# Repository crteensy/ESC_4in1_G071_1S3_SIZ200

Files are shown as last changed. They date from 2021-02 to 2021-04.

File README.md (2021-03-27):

# ESC_4in1_G071_1S3_SIZ200

## UNTESTED
The G071+NCP81161 combo was successfully tested (with PSMN1R8-30MLHX though).

## Important: mounting
The PCB is quite crowded around the mounting holes:
- Do not use M3 metal hardware.
- You can use M3 plastic with slim (5mm outer diameter) standoffs
- You can also use M2 with rubber grommets

## Description
KiCad project for a 20mm 4in1 ESC
- 4 layers for prototyping
- no part smaller than 0402
- 1-3 S
- should be abe to handle 15 A continuous
- STM32G071
- NCP81161 gate drivers
- SIZ200
- 0m5 current sense shunt with INA186A2
- 5V reg: TPS630701; max 2A (VBat = 5 V)

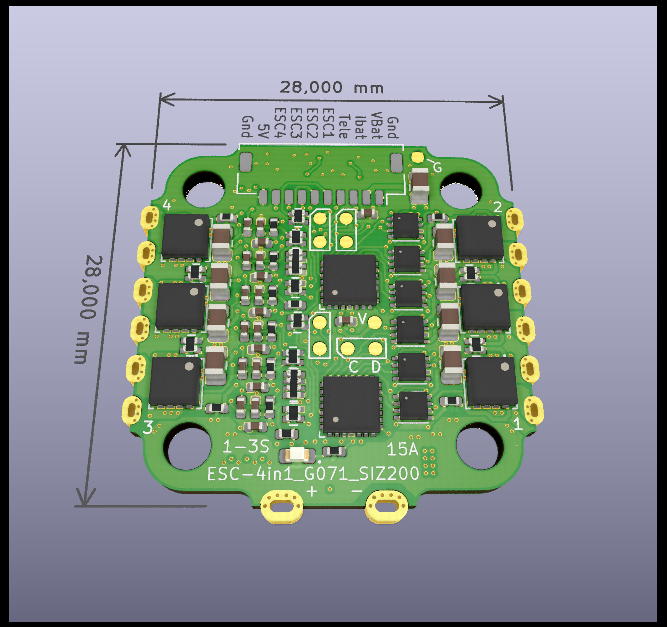
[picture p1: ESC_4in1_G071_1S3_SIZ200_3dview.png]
3D view top


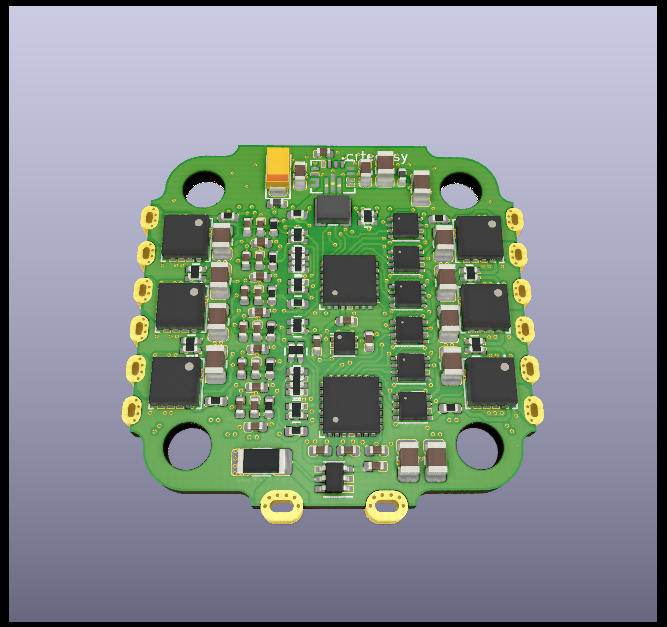
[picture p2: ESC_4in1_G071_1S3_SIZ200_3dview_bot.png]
3D view bottom


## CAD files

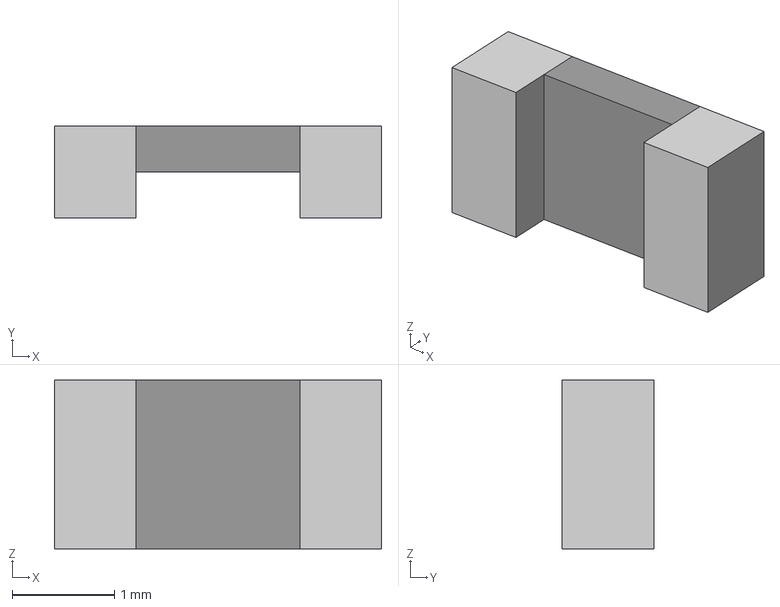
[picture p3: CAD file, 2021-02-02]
backup_20210413_badVias/mod/HCS1206_L500_stp.stp
3.20 x 0.9 x 1.65 mm

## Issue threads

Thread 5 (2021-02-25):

add silk screen for SWD pads

crteensy, 2021-02-25:
clock, data, and ESC# identification are missing for swd pads

Closed 2021-02-27.

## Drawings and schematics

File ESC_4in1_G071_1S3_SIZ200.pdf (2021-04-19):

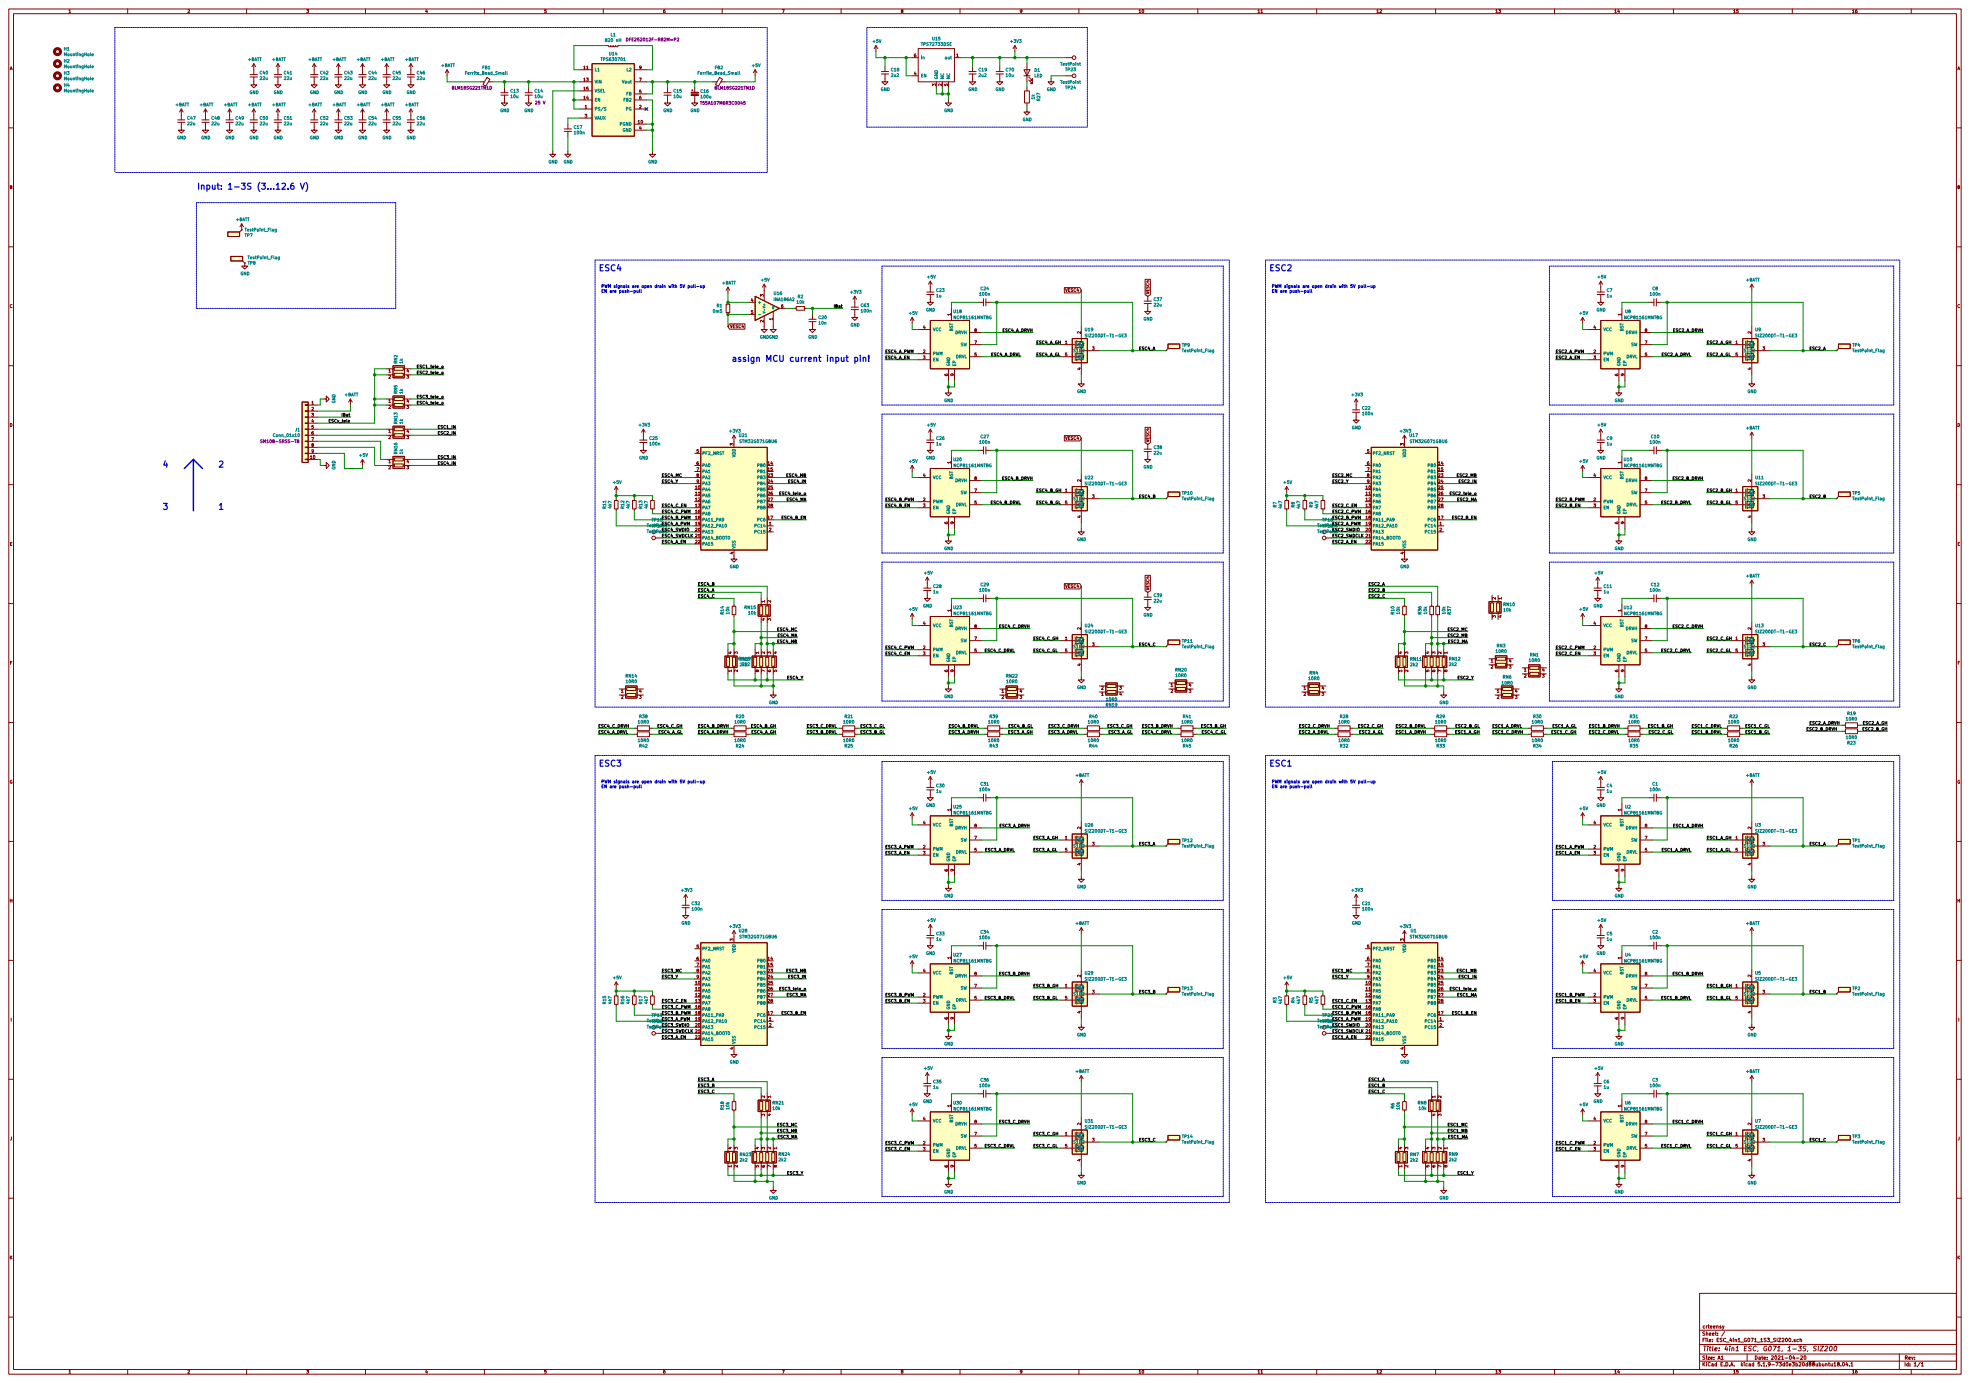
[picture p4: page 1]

PWM signals are open drain with 5V pull-up
EN are push-pull

assign MCU current input pin!

File: ESC_4in1_G071_1S3_SIZ200.sch Sheet: / crteensy

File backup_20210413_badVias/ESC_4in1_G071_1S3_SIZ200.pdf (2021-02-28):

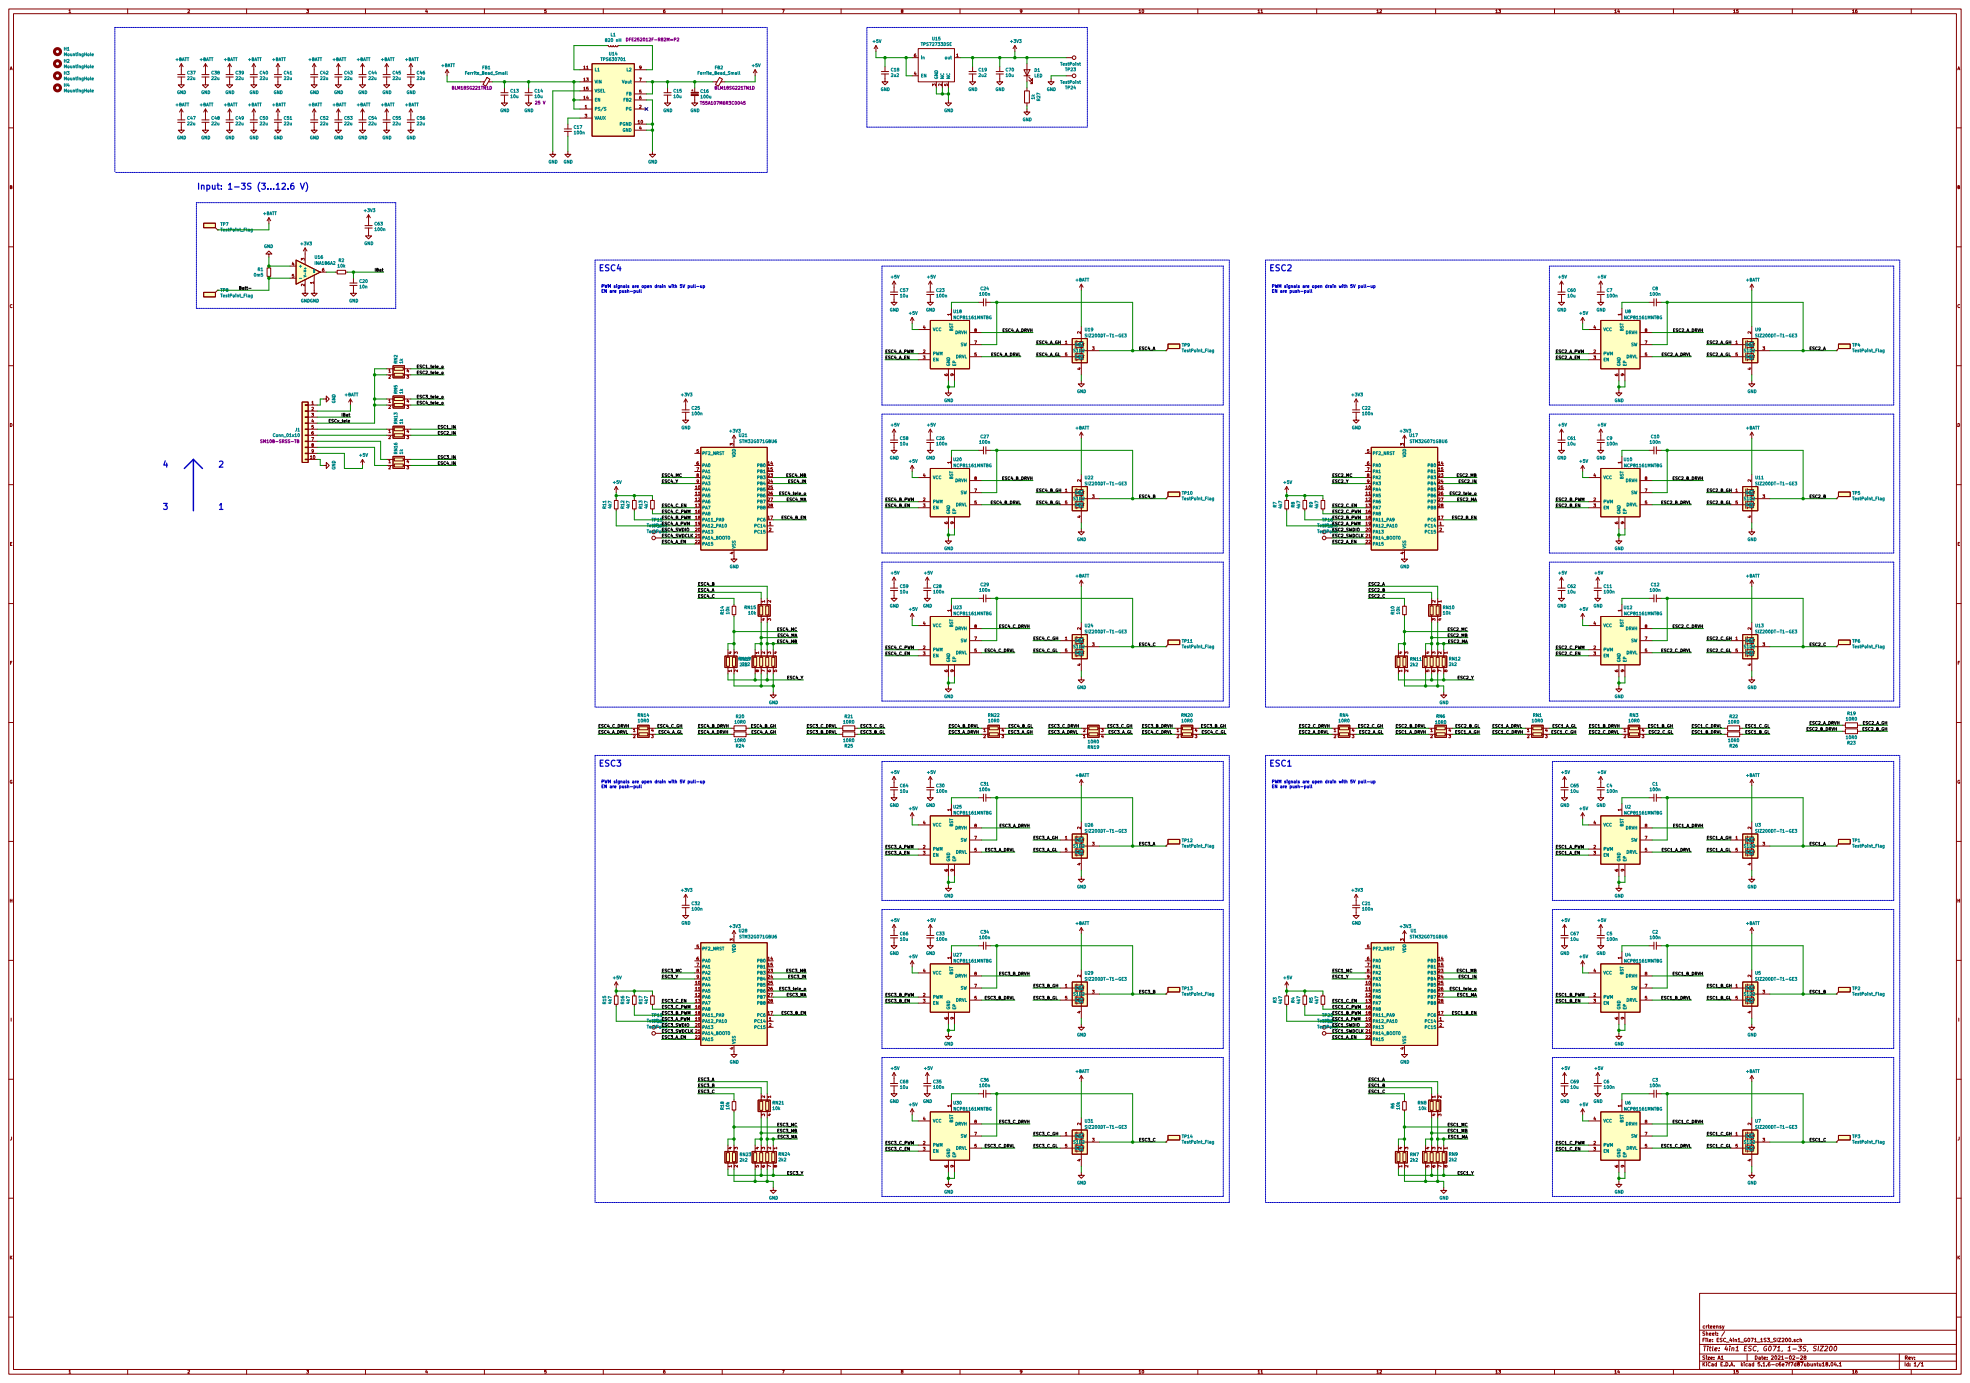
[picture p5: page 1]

PWM signals are open drain with 5V pull-up
EN are push-pull

ESC2_A_GL PWM signals are open drain with 5V pull-up

File: ESC_4in1_G071_1S3_SIZ200.sch Sheet: / crteensy

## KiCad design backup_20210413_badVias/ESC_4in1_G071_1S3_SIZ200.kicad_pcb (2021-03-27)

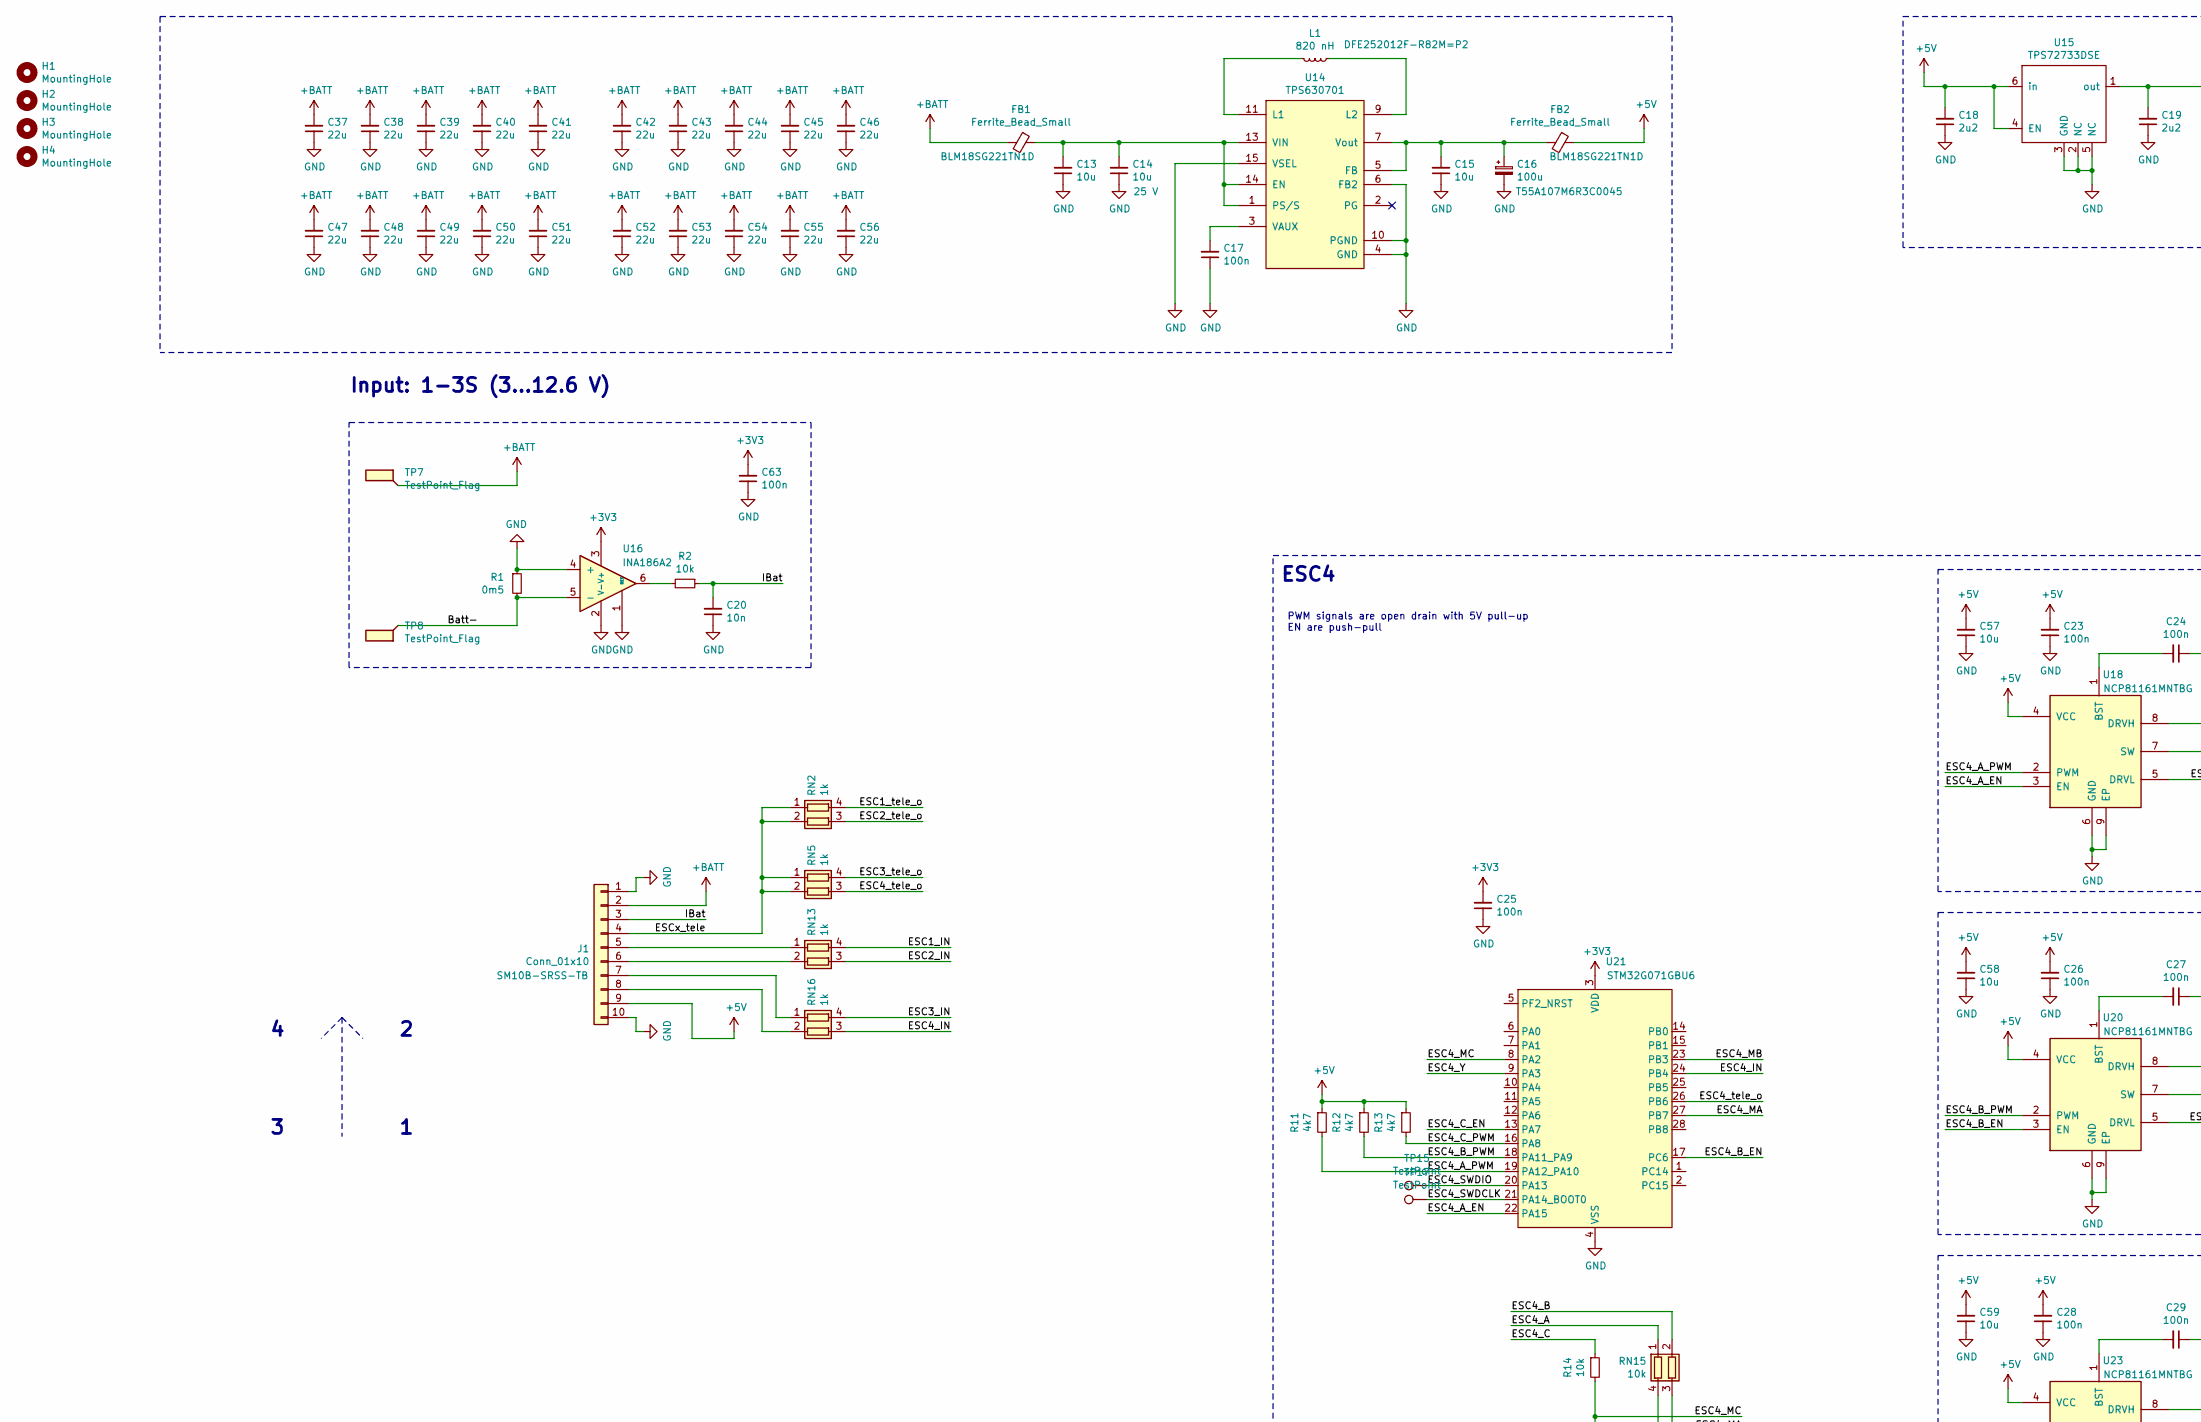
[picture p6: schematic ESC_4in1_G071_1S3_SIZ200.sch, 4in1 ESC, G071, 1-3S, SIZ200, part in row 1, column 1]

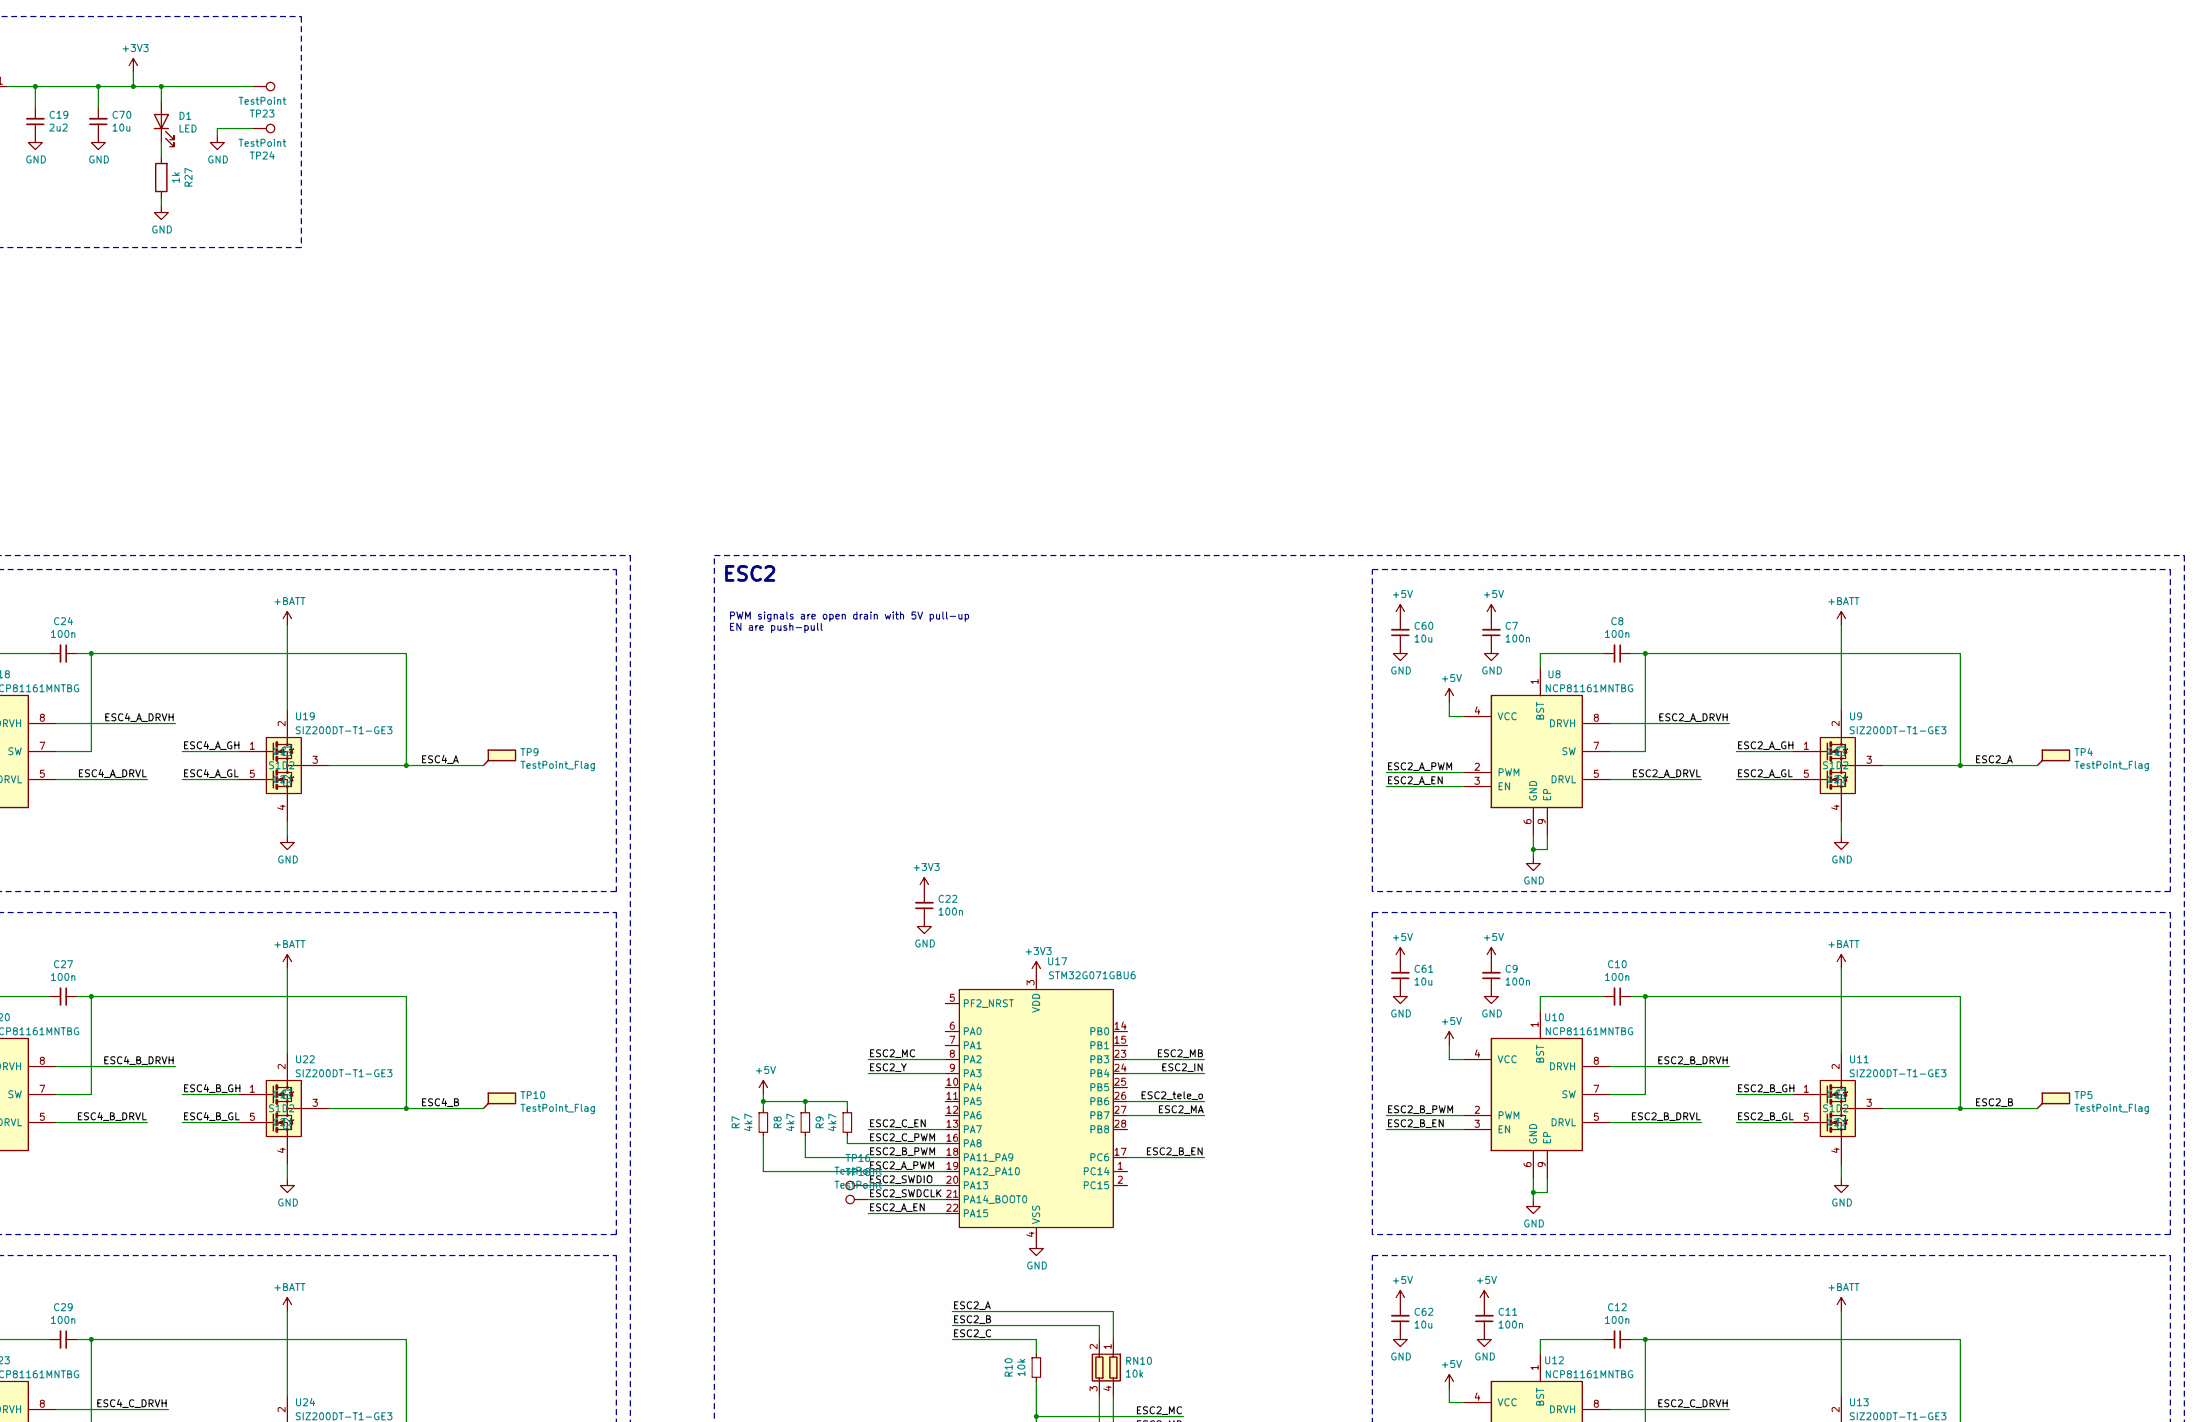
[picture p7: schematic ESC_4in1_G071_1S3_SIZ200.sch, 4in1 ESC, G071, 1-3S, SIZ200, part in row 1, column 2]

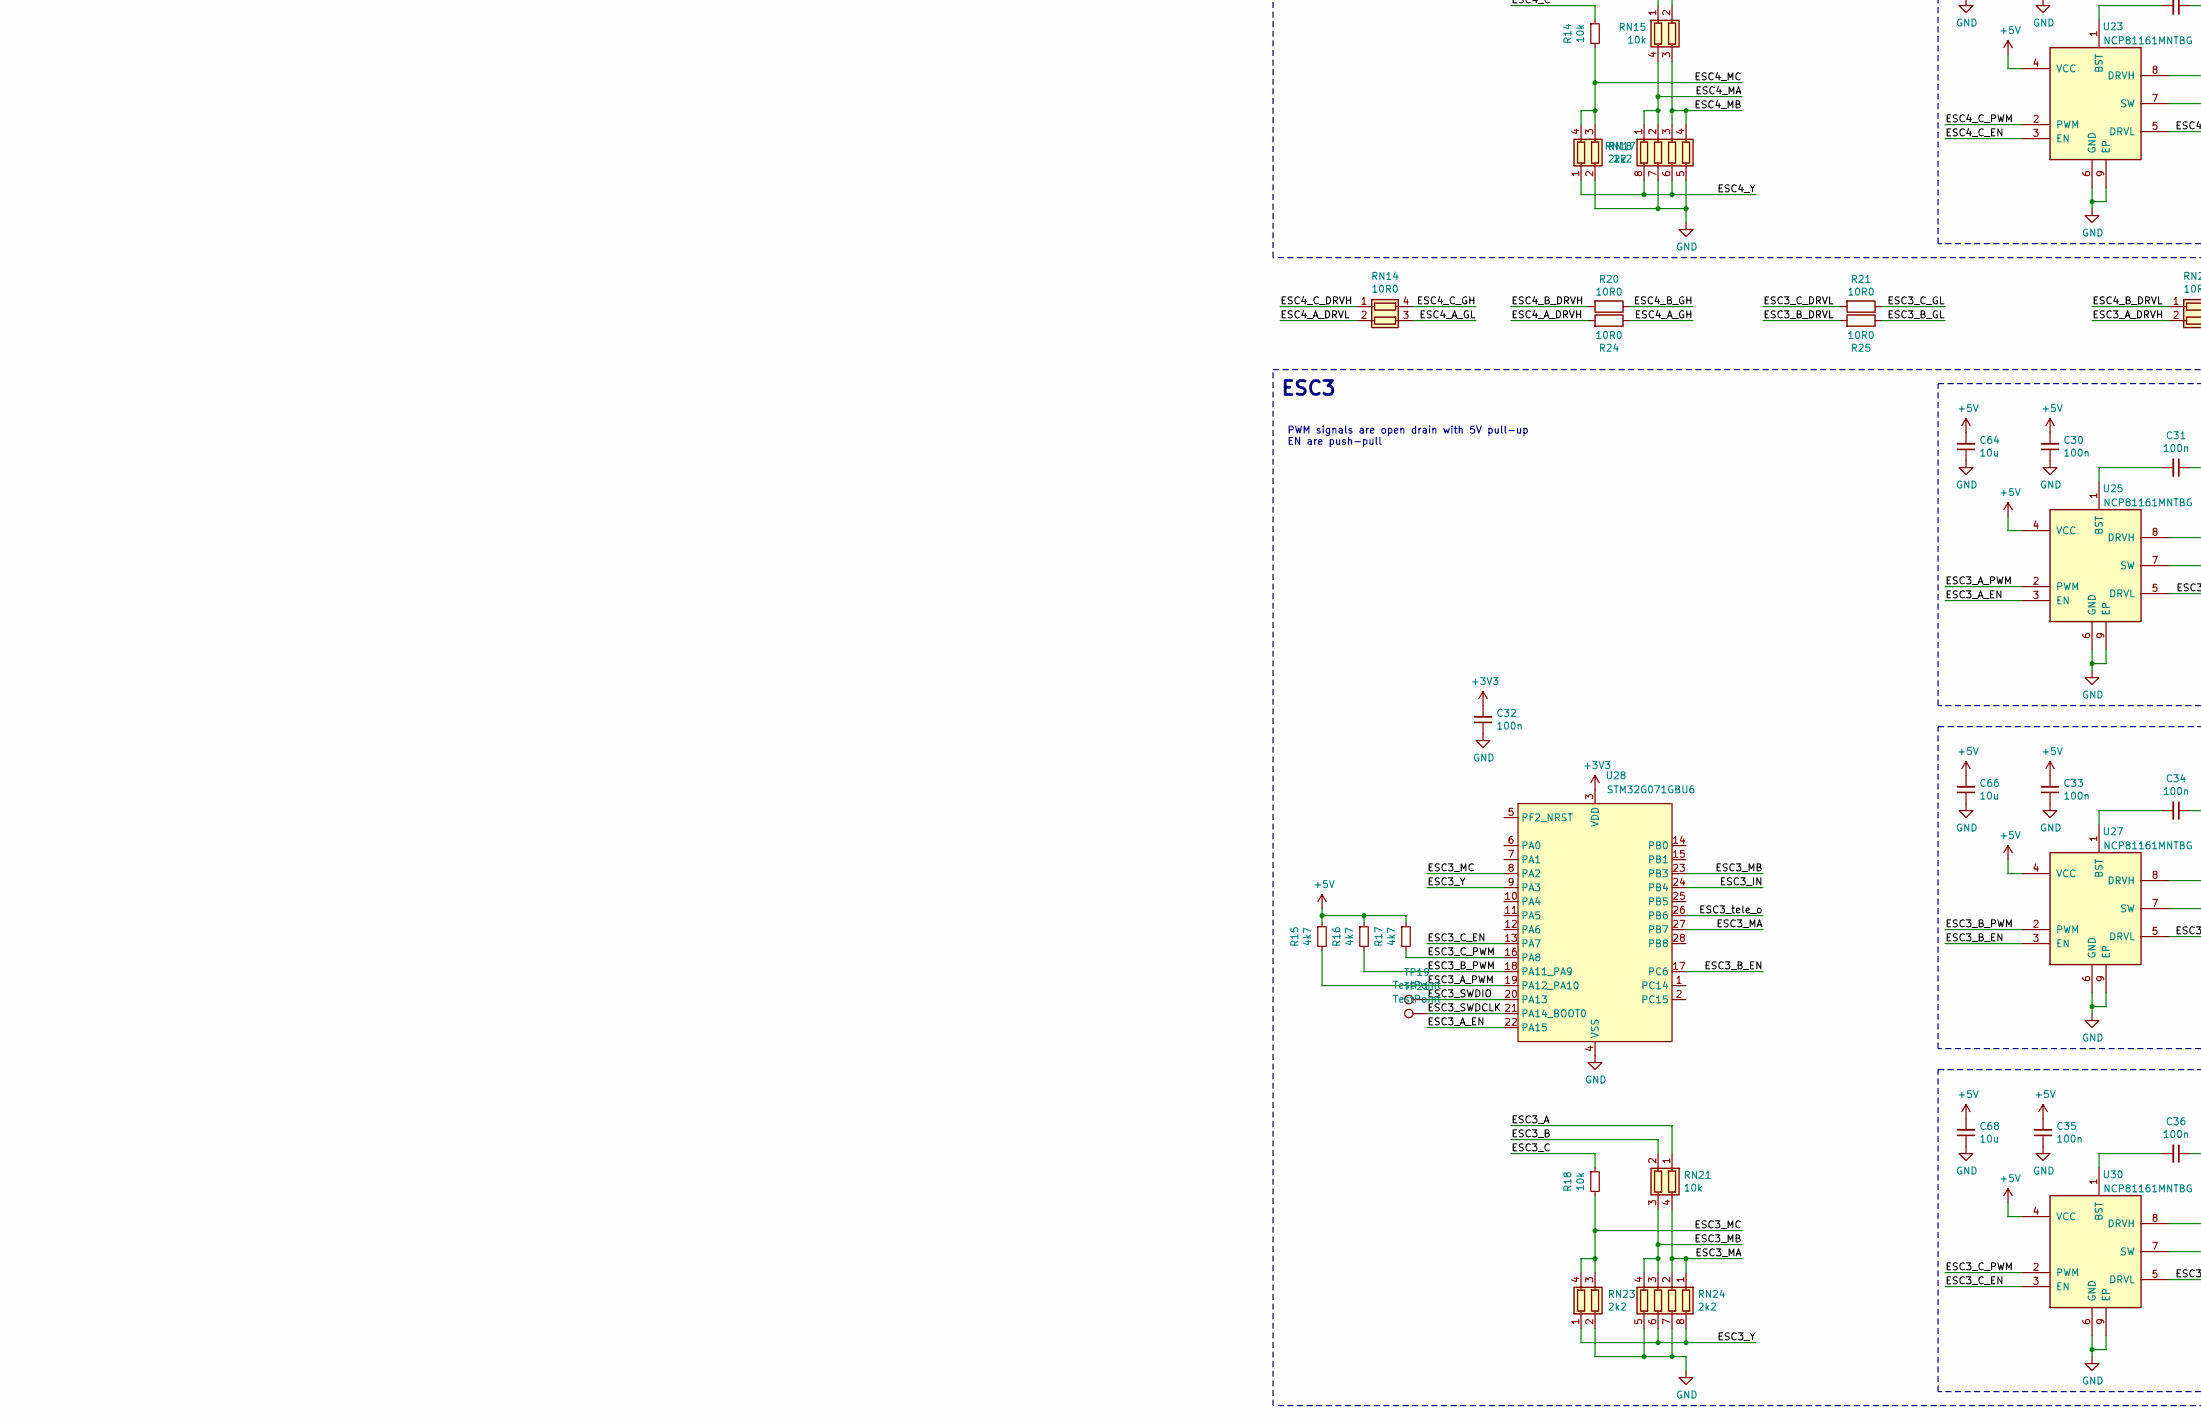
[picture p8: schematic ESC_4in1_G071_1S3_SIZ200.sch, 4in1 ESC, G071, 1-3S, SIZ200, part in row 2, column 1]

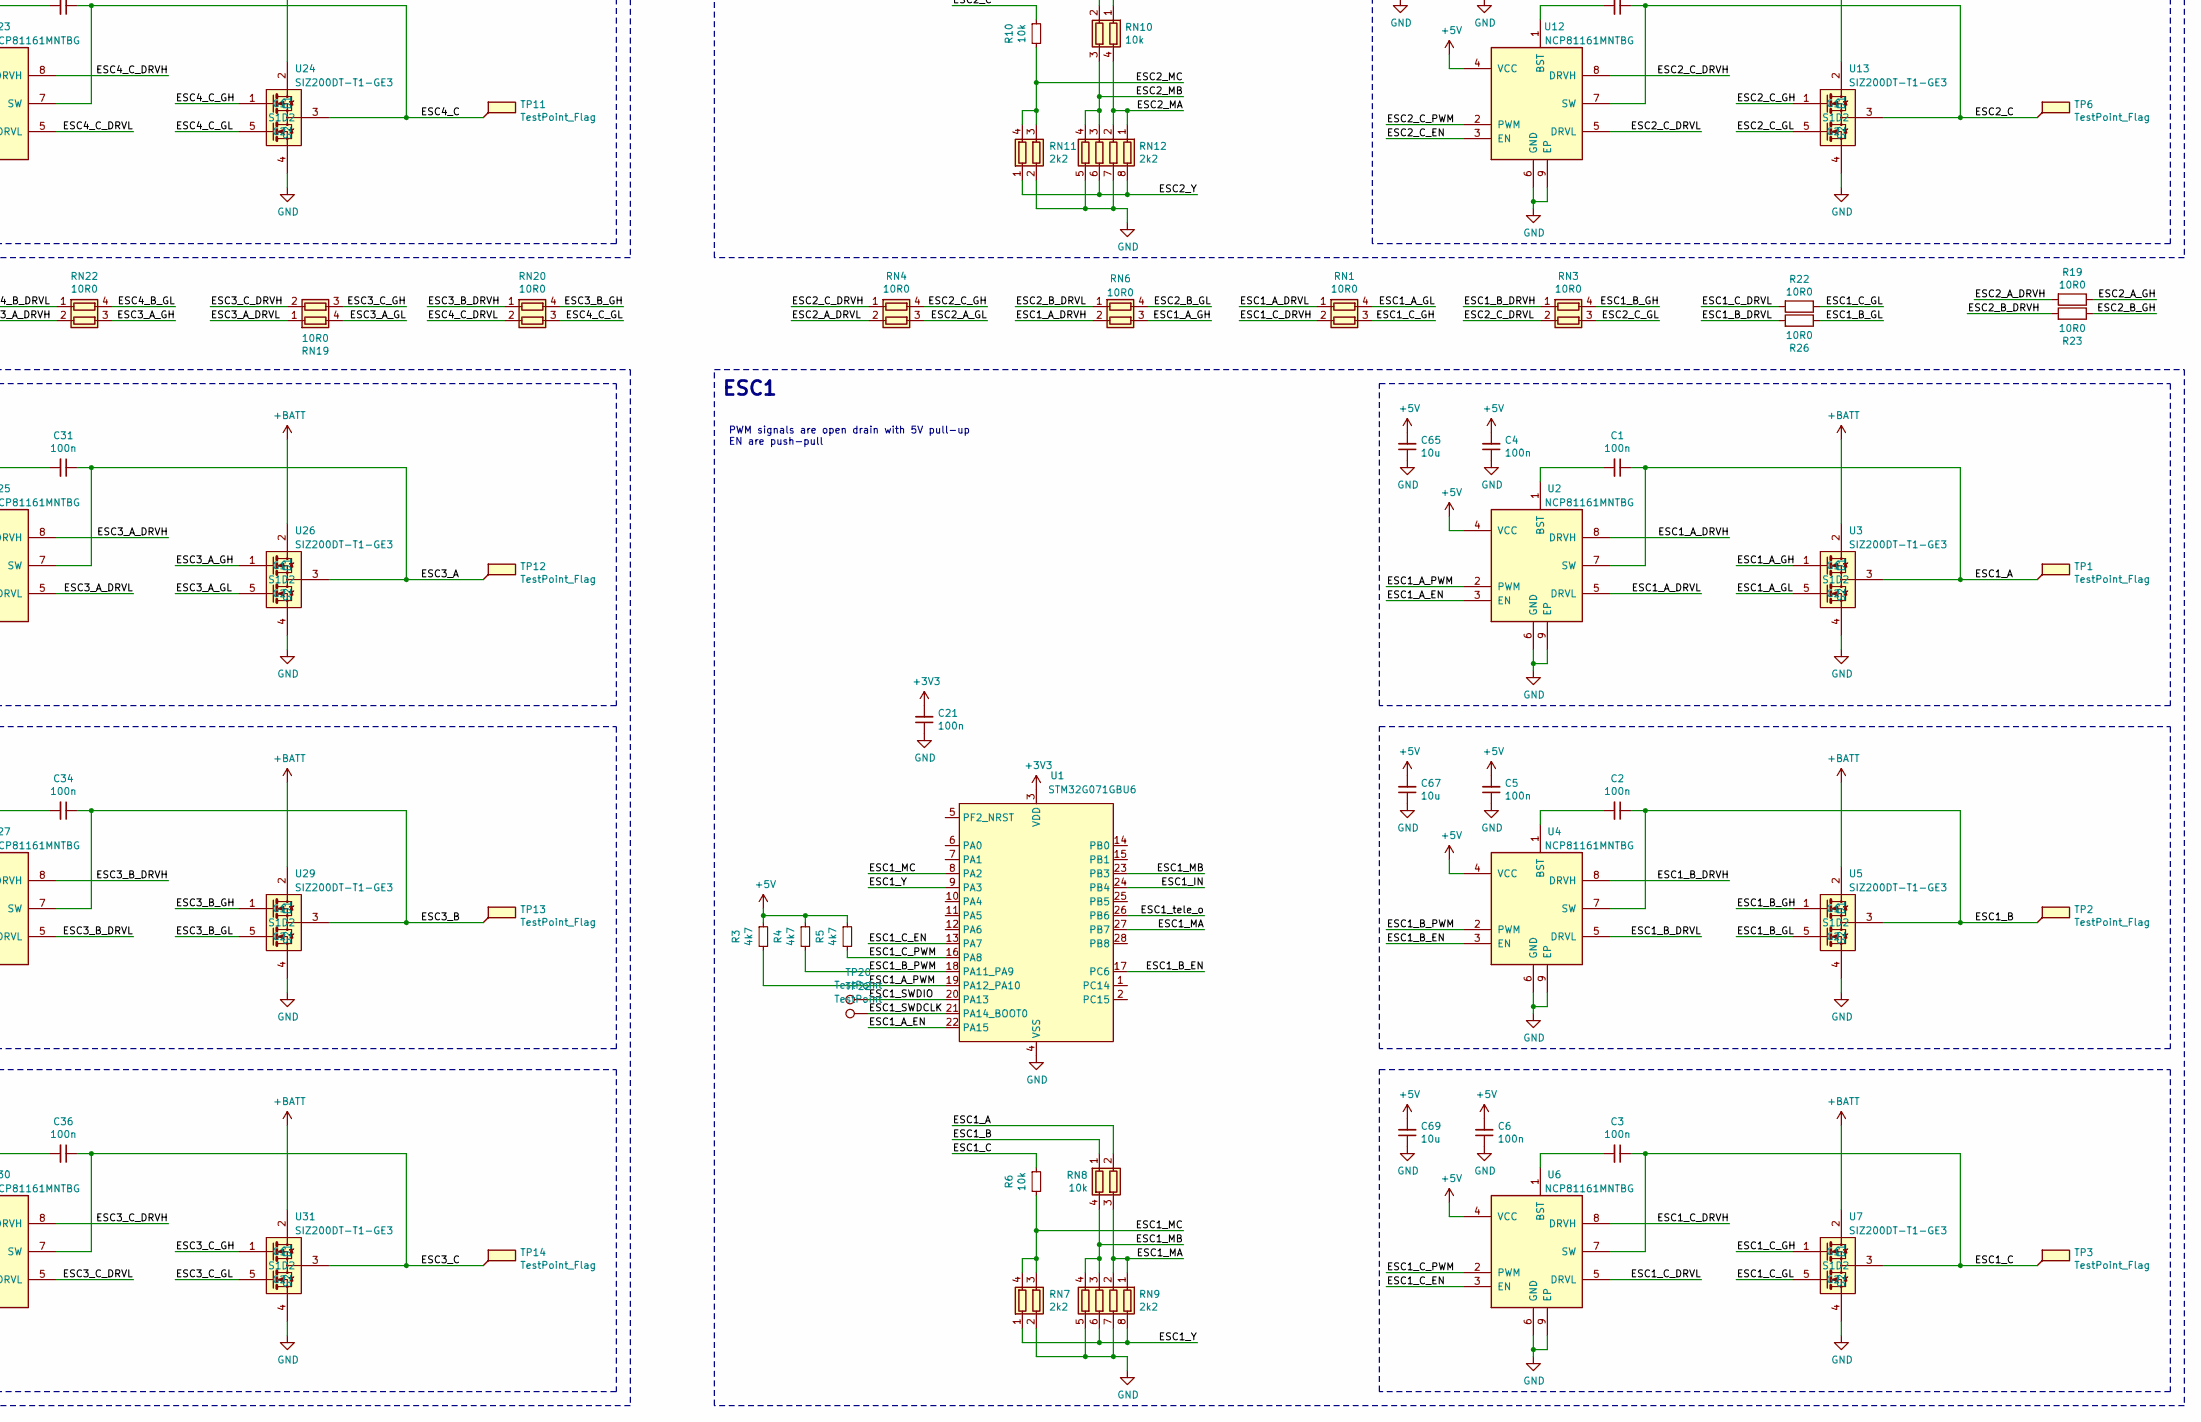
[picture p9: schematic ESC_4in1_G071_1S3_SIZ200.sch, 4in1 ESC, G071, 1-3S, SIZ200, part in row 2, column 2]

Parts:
C1, C2, C3, C4, C5, C6, C7, C8, C9, C10, C11, C12, C17, C21, C22, C23, C24, C25, C26, C27, C28, C29, C30, C31, C32, C33, C34, C35, C36, C63: 100n; C_0402_1005Metric
C13: 10u; C_0805_2012Metric_dense; voltage 25 V
C14: 10u; C_0603_1608Metric_dense; voltage 25 V
C15: 10u; C_0603_1608Metric_dense
C16: 100u; CP_EIA-3216-10_Kemet-I
C18, C19: 2u2; C_0402_1005Metric
C20: 10n; C_0402_1005Metric
C37, C38, C39, C40, C41, C42, C43, C44, C45, C46, C47, C48, C49, C50, C51, C52, C53, C54, C55, C56: 22u; C_0805_2012Metric_dense
C57, C58, C59, C60, C61, C62, C64, C65, C66, C67, C68, C69, C70: 10u; C_0402_1005Metric
D1: LED; LED_0603_1608Metric
FB1, FB2: Ferrite_Bead_Small; L_0402_1005Metric
H1, H2, H3, H4: MountingHole; MountingHole_3.2mm_4mm
J1: Conn_01x10; JST_SHL_SM10B-SHLS-TF_1x10-1MP_P1.00mm_Horizontal_dense
L1: 820 nH; L_Wuerth_MAPI-2510
R1: 0m5; R_1206_3216Metric
R2, R6, R10, R14, R18: 10k; R_0402_1005Metric
R3, R4, R5, R7, R8, R9, R11, R12, R13, R15, R16, R17: 4k7; R_0402_1005Metric
R19, R20, R21, R22, R23, R24, R25, R26: 10R0; R_0402_1005Metric
R27: 1k; R_0402_1005Metric
RN1, RN3, RN4, RN6, RN14, RN19, RN20, RN22: 10R0; R_Array_Convex_2x0402_dense
RN2, RN5, RN13, RN16: 1k; R_Array_Convex_2x0402_dense
RN7, RN11, RN17, RN23: 2k2; R_Array_Convex_2x0402_dense
RN8, RN10, RN15, RN21: 10k; R_Array_Convex_2x0402_dense
RN9, RN12, RN18, RN24: 2k2; R_Array_Convex_4x0402_dense
TP1, TP2, TP3, TP4, TP5, TP6, TP9, TP10, TP11, TP12, TP13, TP14: TestPoint_Flag; esc_pad_relaxed_n4
TP7, TP8: TestPoint_Flag; batt_pad_wide_relaxed
TP15, TP16, TP17, TP18, TP19, TP20, TP21, TP22, TP23, TP24: TestPoint; TestPoint_Pad_D1.0mm_dense
U1, U17, U21, U28: STM32G071GBU6; UFQFPN28
U2, U4, U6, U8, U10, U12, U18, U20, U23, U25, U27, U30: NCP81161MNTBG; DFN-8-1EP_2x2mm_P0.5mm_EP0.9x1.3mm_narrow
U3, U5, U7, U9, U11, U13, U19, U22, U24, U26, U29, U31: SIZ200DT-T1-GE3; PowerPAIR3.3x3.3_splitpaste
U14: TPS630701; TEXAS_15-VQFN-HR
U15: TPS72733DSE; WSON-6_1.5x1.5mm_P0.5mm
U16: INA186A2; SOT-363_SC-70-6

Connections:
+3V3: C19.2, C21.2, C22.2, C25.2, C32.2, C63.2, C70.2, D1.2 (A), TP23.1, U1.3 (VDD), U15.1 (out), U16.3 (V+), U17.3 (VDD), U21.3 (VDD), U28.3 (VDD)
+5V: C4.2, C5.2, C6.2, C7.2, C9.2, C11.2, C18.2, C23.2, C26.2, C28.2, C30.2, C33.2, C35.2, C57.2, C58.2, C59.2, C60.2, C61.2, C62.2, C64.2, C65.2, C66.2, C67.2, C68.2, C69.2, FB2.1, J1.9, R3.1, R4.1, R5.1, R7.1, R8.1, R9.1, R11.1, R12.1, R13.1, R15.1, R16.1, R17.1, U2.4 (VCC), U4.4 (VCC), U6.4 (VCC), U8.4 (VCC), U10.4 (VCC), U12.4 (VCC), U15.4 (EN), U15.6 (in), U18.4 (VCC), U20.4 (VCC), U23.4 (VCC), U25.4 (VCC), U27.4 (VCC), U30.4 (VCC)
+BATT: C37.2, C38.2, C39.2, C40.2, C41.2, C42.2, C43.2, C44.2, C45.2, C46.2, C47.2, C48.2, C49.2, C50.2, C51.2, C52.2, C53.2, C54.2, C55.2, C56.2, FB1.2, J1.2, TP7.1, U3.2 (D1), U5.2 (D1), U7.2 (D1), U9.2 (D1), U11.2 (D1), U13.2 (D1), U19.2 (D1), U22.2 (D1), U24.2 (D1), U26.2 (D1), U29.2 (D1), U31.2 (D1)
/Batt-: R1.2, TP8.1, U16.5 (-)
/ESC1_A: C1.1, RN8.2 (R2.1), TP1.1, U2.7 (SW), U3.3 (S1D2)
/ESC1_A_DRVH: RN6.2 (R2.1), U2.8 (DRVH)
/ESC1_A_DRVL: RN1.1 (R1.1), U2.5 (DRVL)
/ESC1_A_EN: U1.22 (PA15), U2.3 (EN)
/ESC1_A_GH: RN6.3 (R2.2), U3.1 (G1)
/ESC1_A_GL: RN1.4 (R1.2), U3.5 (G2)
/ESC1_A_PWM: R3.2, U1.19 (PA12_PA10), U2.2 (PWM)
/ESC1_B: C2.1, RN8.1 (R1.1), TP2.1, U4.7 (SW), U5.3 (S1D2)
/ESC1_B_DRVH: RN3.1 (R1.1), U4.8 (DRVH)
/ESC1_B_DRVL: R26.2, U4.5 (DRVL)
/ESC1_B_EN: U1.17 (PC6), U4.3 (EN)
/ESC1_B_GH: RN3.4 (R1.2), U5.1 (G1)
/ESC1_B_GL: R26.1, U5.5 (G2)
/ESC1_B_PWM: R4.2, U1.18 (PA11_PA9), U4.2 (PWM)
/ESC1_C: C3.1, R6.1, TP3.1, U6.7 (SW), U7.3 (S1D2)
/ESC1_C_DRVH: RN1.2 (R2.1), U6.8 (DRVH)
/ESC1_C_DRVL: R22.2, U6.5 (DRVL)
/ESC1_C_EN: U1.13 (PA7), U6.3 (EN)
/ESC1_C_GH: RN1.3 (R2.2), U7.1 (G1)
/ESC1_C_GL: R22.1, U7.5 (G2)
/ESC1_C_PWM: R5.2, U1.16 (PA8), U6.2 (PWM)
/ESC1_IN: RN13.4 (R1.2), U1.24 (PB4)
/ESC1_MA: RN8.3 (R2.2), RN9.1 (R1.1), RN9.2 (R2.1), U1.27 (PB7)
/ESC1_MB: RN8.4 (R1.2), RN9.3 (R3.1), RN9.4 (R4.1), U1.23 (PB3)
/ESC1_MC: R6.2, RN7.3 (R2.2), RN7.4 (R1.2), U1.8 (PA2)
/ESC1_SWDCLK: TP22.1, U1.21 (PA14_BOOT0)
/ESC1_SWDIO: TP20.1, U1.20 (PA13)
/ESC1_Y: RN7.1 (R1.1), RN9.6 (R3.2), RN9.8 (R1.2), U1.9 (PA3)
/ESC1_tele_o: RN2.4 (R1.2), U1.26 (PB6)
/ESC2_A: C8.1, RN10.1 (R1.1), TP4.1, U8.7 (SW), U9.3 (S1D2)
/ESC2_A_DRVH: R19.2, U8.8 (DRVH)
/ESC2_A_DRVL: RN4.2 (R2.1), U8.5 (DRVL)
/ESC2_A_EN: U8.3 (EN), U17.22 (PA15)
/ESC2_A_GH: R19.1, U9.1 (G1)
/ESC2_A_GL: RN4.3 (R2.2), U9.5 (G2)
/ESC2_A_PWM: R7.2, U8.2 (PWM), U17.19 (PA12_PA10)
/ESC2_B: C10.1, RN10.2 (R2.1), TP5.1, U10.7 (SW), U11.3 (S1D2)
/ESC2_B_DRVH: R23.2, U10.8 (DRVH)
/ESC2_B_DRVL: RN6.1 (R1.1), U10.5 (DRVL)
/ESC2_B_EN: U10.3 (EN), U17.17 (PC6)
/ESC2_B_GH: R23.1, U11.1 (G1)
/ESC2_B_GL: RN6.4 (R1.2), U11.5 (G2)
/ESC2_B_PWM: R8.2, U10.2 (PWM), U17.18 (PA11_PA9)
/ESC2_C: C12.1, R10.1, TP6.1, U12.7 (SW), U13.3 (S1D2)
/ESC2_C_DRVH: RN4.1 (R1.1), U12.8 (DRVH)
/ESC2_C_DRVL: RN3.2 (R2.1), U12.5 (DRVL)
/ESC2_C_EN: U12.3 (EN), U17.13 (PA7)
/ESC2_C_GH: RN4.4 (R1.2), U13.1 (G1)
/ESC2_C_GL: RN3.3 (R2.2), U13.5 (G2)
/ESC2_C_PWM: R9.2, U12.2 (PWM), U17.16 (PA8)
/ESC2_IN: RN13.3 (R2.2), U17.24 (PB4)
/ESC2_MA: RN10.4 (R1.2), RN12.1 (R1.1), RN12.2 (R2.1), U17.27 (PB7)
/ESC2_MB: RN10.3 (R2.2), RN12.3 (R3.1), RN12.4 (R4.1), U17.23 (PB3)
/ESC2_MC: R10.2, RN11.3 (R2.2), RN11.4 (R1.2), U17.8 (PA2)
/ESC2_SWDCLK: TP18.1, U17.21 (PA14_BOOT0)
/ESC2_SWDIO: TP16.1, U17.20 (PA13)
/ESC2_Y: RN11.1 (R1.1), RN12.6 (R3.2), RN12.8 (R1.2), U17.9 (PA3)
/ESC2_tele_o: RN2.3 (R2.2), U17.26 (PB6)
/ESC3_A: C31.1, RN21.1 (R1.1), TP12.1, U25.7 (SW), U26.3 (S1D2)
/ESC3_A_DRVH: RN22.2 (R2.1), U25.8 (DRVH)
/ESC3_A_DRVL: RN19.1 (R1.1), U25.5 (DRVL)
/ESC3_A_EN: U25.3 (EN), U28.22 (PA15)
/ESC3_A_GH: RN22.3 (R2.2), U26.1 (G1)
/ESC3_A_GL: RN19.4 (R1.2), U26.5 (G2)
/ESC3_A_PWM: R15.2, U25.2 (PWM), U28.19 (PA12_PA10)
/ESC3_B: C34.1, RN21.2 (R2.1), TP13.1, U27.7 (SW), U29.3 (S1D2)
/ESC3_B_DRVH: RN20.1 (R1.1), U27.8 (DRVH)
/ESC3_B_DRVL: R25.2, U27.5 (DRVL)
/ESC3_B_EN: U27.3 (EN), U28.17 (PC6)
/ESC3_B_GH: RN20.4 (R1.2), U29.1 (G1)
/ESC3_B_GL: R25.1, U29.5 (G2)
/ESC3_B_PWM: R16.2, U27.2 (PWM), U28.18 (PA11_PA9)
/ESC3_C: C36.1, R18.1, TP14.1, U30.7 (SW), U31.3 (S1D2)
/ESC3_C_DRVH: RN19.2 (R2.1), U30.8 (DRVH)
/ESC3_C_DRVL: R21.2, U30.5 (DRVL)
/ESC3_C_EN: U28.13 (PA7), U30.3 (EN)
/ESC3_C_GH: RN19.3 (R2.2), U31.1 (G1)
/ESC3_C_GL: R21.1, U31.5 (G2)
/ESC3_C_PWM: R17.2, U28.16 (PA8), U30.2 (PWM)
/ESC3_IN: RN16.4 (R1.2), U28.24 (PB4)
/ESC3_MA: RN21.4 (R1.2), RN24.1 (R1.1), RN24.2 (R2.1), U28.27 (PB7)
/ESC3_MB: RN21.3 (R2.2), RN24.3 (R3.1), RN24.4 (R4.1), U28.23 (PB3)
/ESC3_MC: R18.2, RN23.3 (R2.2), RN23.4 (R1.2), U28.8 (PA2)
/ESC3_SWDCLK: TP21.1, U28.21 (PA14_BOOT0)
/ESC3_SWDIO: TP19.1, U28.20 (PA13)
/ESC3_Y: RN23.1 (R1.1), RN24.6 (R3.2), RN24.8 (R1.2), U28.9 (PA3)
/ESC3_tele_o: RN5.4 (R1.2), U28.26 (PB6)
/ESC4_A: C24.1, RN15.1 (R1.1), TP9.1, U18.7 (SW), U19.3 (S1D2)
/ESC4_A_DRVH: R24.2, U18.8 (DRVH)
/ESC4_A_DRVL: RN14.2 (R2.1), U18.5 (DRVL)
/ESC4_A_EN: U18.3 (EN), U21.22 (PA15)
/ESC4_A_GH: R24.1, U19.1 (G1)
/ESC4_A_GL: RN14.3 (R2.2), U19.5 (G2)
/ESC4_A_PWM: R11.2, U18.2 (PWM), U21.19 (PA12_PA10)
/ESC4_B: C27.1, RN15.2 (R2.1), TP10.1, U20.7 (SW), U22.3 (S1D2)
/ESC4_B_DRVH: R20.2, U20.8 (DRVH)
/ESC4_B_DRVL: RN22.1 (R1.1), U20.5 (DRVL)
/ESC4_B_EN: U20.3 (EN), U21.17 (PC6)
/ESC4_B_GH: R20.1, U22.1 (G1)
/ESC4_B_GL: RN22.4 (R1.2), U22.5 (G2)
/ESC4_B_PWM: R12.2, U20.2 (PWM), U21.18 (PA11_PA9)
/ESC4_C: C29.1, R14.1, TP11.1, U23.7 (SW), U24.3 (S1D2)
/ESC4_C_DRVH: RN14.1 (R1.1), U23.8 (DRVH)
/ESC4_C_DRVL: RN20.2 (R2.1), U23.5 (DRVL)
/ESC4_C_EN: U21.13 (PA7), U23.3 (EN)
/ESC4_C_GH: RN14.4 (R1.2), U24.1 (G1)
/ESC4_C_GL: RN20.3 (R2.2), U24.5 (G2)
/ESC4_C_PWM: R13.2, U21.16 (PA8), U23.2 (PWM)
/ESC4_IN: RN16.3 (R2.2), U21.24 (PB4)
/ESC4_MA: RN15.4 (R1.2), RN18.1 (R1.1), RN18.2 (R2.1), U21.27 (PB7)
/ESC4_MB: RN15.3 (R2.2), RN18.3 (R3.1), RN18.4 (R4.1), U21.23 (PB3)
/ESC4_MC: R14.2, RN17.3 (R2.2), RN17.4 (R1.2), U21.8 (PA2)
/ESC4_SWDCLK: TP17.1, U21.21 (PA14_BOOT0)
/ESC4_SWDIO: TP15.1, U21.20 (PA13)
/ESC4_Y: RN17.1 (R1.1), RN18.6 (R3.2), RN18.8 (R1.2), U21.9 (PA3)
/ESC4_tele_o: RN5.3 (R2.2), U21.26 (PB6)
/ESCx_tele: J1.4, RN2.1 (R1.1), RN2.2 (R2.1), RN5.1 (R1.1), RN5.2 (R2.1)
/IBat: C20.2, J1.3, R2.1
GND: C4.1, C5.1, C6.1, C7.1, C9.1, C11.1, C13.1, C14.1, C15.1, C16.2, C17.1, C18.1, C19.1, C20.1, C21.1, C22.1, C23.1, C25.1, C26.1, C28.1, C30.1, C32.1, C33.1, C35.1, C37.1, C38.1, C39.1, C40.1, C41.1, C42.1, C43.1, C44.1, C45.1, C46.1, C47.1, C48.1, C49.1, C50.1, C51.1, C52.1, C53.1, C54.1, C55.1, C56.1, C57.1, C58.1, C59.1, C60.1, C61.1, C62.1, C63.1, C64.1, C65.1, C66.1, C67.1, C68.1, C69.1, C70.1, J1.1, J1.10, R1.1, R27.1, RN7.2 (R2.1), RN9.5 (R4.2), RN9.7 (R2.2), RN11.2 (R2.1), RN12.5 (R4.2), RN12.7 (R2.2), RN17.2 (R2.1), RN18.5 (R4.2), RN18.7 (R2.2), RN23.2 (R2.1), RN24.5 (R4.2), RN24.7 (R2.2), TP24.1, U1.4 (VSS), U2.6 (GND), U2.9 (EP), U3.4 (S2), U4.6 (GND), U4.9 (EP), U5.4 (S2), U6.6 (GND), U6.9 (EP), U7.4 (S2), U8.6 (GND), U8.9 (EP), U9.4 (S2), U10.6 (GND), U10.9 (EP), U11.4 (S2), U12.6 (GND), U12.9 (EP), U13.4 (S2), U14.4 (GND), U14.6 (FB2), U14.10 (PGND), U14.15 (VSEL), U15.2 (NC), U15.3 (GND), U15.5 (NC), U16.1 (REF), U16.2 (V-), U16.4 (+), U17.4 (VSS), U18.6 (GND), U18.9 (EP), U19.4 (S2), U20.6 (GND), U20.9 (EP), U21.4 (VSS), U22.4 (S2), U23.6 (GND), U23.9 (EP), U24.4 (S2), U25.6 (GND), U25.9 (EP), U26.4 (S2), U27.6 (GND), U27.9 (EP), U28.4 (VSS), U29.4 (S2), U30.6 (GND), U30.9 (EP), U31.4 (S2)
unnamed: C1.2, U2.1 (BST)
unnamed: C2.2, U4.1 (BST)
unnamed: C3.2, U6.1 (BST)
unnamed: C8.2, U8.1 (BST)
unnamed: C10.2, U10.1 (BST)
unnamed: C12.2, U12.1 (BST)
unnamed: C13.2, C14.2, FB1.1, U14.1 (PS/S), U14.13 (VIN), U14.14 (EN)
unnamed: C15.2, C16.1, FB2.2, U14.5 (FB), U14.7 (Vout)
unnamed: C17.2, U14.3 (VAUX)
unnamed: C24.2, U18.1 (BST)
unnamed: C27.2, U20.1 (BST)
unnamed: C29.2, U23.1 (BST)
unnamed: C31.2, U25.1 (BST)
unnamed: C34.2, U27.1 (BST)
unnamed: C36.2, U30.1 (BST)
unnamed: D1.1 (K), R27.2
unnamed: J1.5, RN13.1 (R1.1)
unnamed: J1.6, RN13.2 (R2.1)
unnamed: J1.7, RN16.1 (R1.1)
unnamed: J1.8, RN16.2 (R2.1)
unnamed: L1.1, U14.9 (L2)
unnamed: L1.2, U14.11 (L1)
unnamed: R2.2, U16.6

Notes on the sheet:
ESC1
PWM signals are open drain with 5V pull-up EN are push-pull
ESC2
ESC3
ESC4
Input: 1-3S (3...12.6 V)

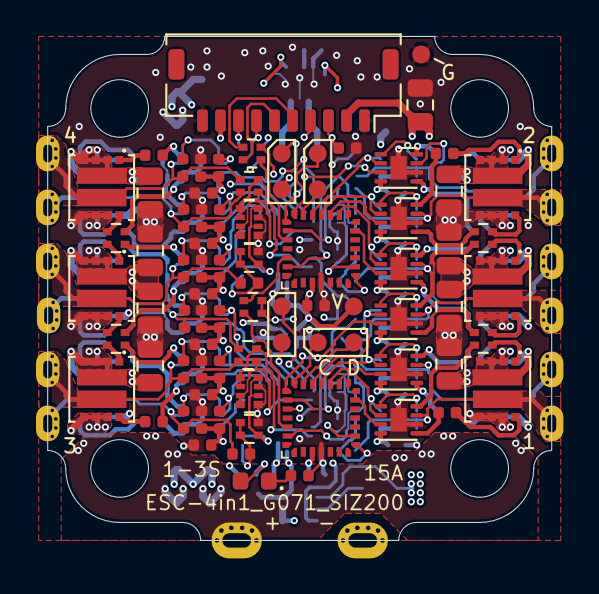
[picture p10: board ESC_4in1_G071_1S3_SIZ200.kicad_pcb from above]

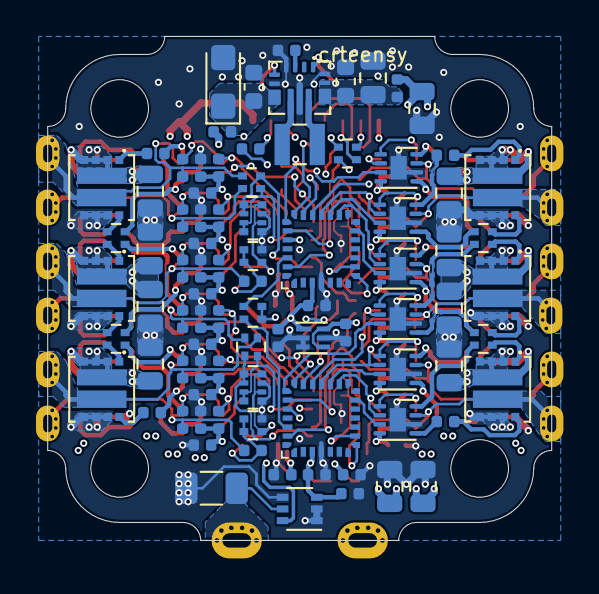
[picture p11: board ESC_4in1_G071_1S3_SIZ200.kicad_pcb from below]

Board: 4 copper layers, 28.0 x 28.0 mm, 185 parts (87 on the bottom side), 146 nets.

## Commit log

2021-01-26 update schematic and layout
    [ESC_4in1_G071_1S3_SIZ200.kicad_pcb, ESC_4in1_G071_1S3_SIZ200.sch, ESC_4in1_G071_1S3_SIZ200_LayoutA.kicad_pcb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]
2021-01-31 update schematic
    [ESC_4in1_G071_1S3_SIZ200.kicad_pcb, ESC_4in1_G071_1S3_SIZ200.sch]
2021-02-01 - ESC1 pinout updated - ESC1 schematic done - ESC1 routed - increased PCB size to 26*27 mm
    [ESC_4in1_G071_1S3_SIZ200.sch, ESC_4in1_G071_1S3_SIZ200_LayoutB_90deg.kicad_pcb]
2021-02-01 - update schematic pdf
2021-02-10 update schematic pdf
2021-02-16 update design files
    [ESC_4in1_G071_1S3_SIZ200.kicad_pcb, ESC_4in1_G071_1S3_SIZ200.sch]
2021-02-20 update layout
    [ESC_4in1_G071_1S3_SIZ200.kicad_pcb, SM08B-SRSS-TB(LF)(SN)--3DModel-STEP-56544.STEP]
2021-02-20 update schematic, layout and schematic pdf
    [ESC_4in1_G071_1S3_SIZ200.kicad_pcb, ESC_4in1_G071_1S3_SIZ200.sch]
2021-02-20 remove backup layouts
    [ESC_4in1_G071_1S3_SIZ200_LayoutA.kicad_pcb, ESC_4in1_G071_1S3_SIZ200_LayoutB.kicad_pcb, ESC_4in1_G071_1S3_SIZ200_LayoutC.kicad_pcb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]
2021-02-25 cosmetic update
    [ESC_4in1_G071_1S3_SIZ200.kicad_pcb, ESC_4in1_G071_1S3_SIZ200.sch]
2021-02-27 update schematic, layout and doc
    [ESC_4in1_G071_1S3_SIZ200.kicad_pcb, ESC_4in1_G071_1S3_SIZ200.sch, ESC_4in1_G071_1S3_SIZ200_20210222_2340.kicad_pcb]
2021-02-28 minor cosmetic updates
    [ESC_4in1_G071_1S3_SIZ200.kicad_pcb, ESC_4in1_G071_1S3_SIZ200.sch]
2021-02-28 remove extra files
    [ESC_4in1_G071_1S3_SIZ200_20210222_2340.kicad_pcb, TPS630701_values.ods]
2021-03-03 layout cosmetics
    [ESC_4in1_G071_1S3_SIZ200.kicad_pcb]
2021-03-05 layout cosmetics, new 3D view files
    [ESC_4in1_G071_1S3_SIZ200.kicad_pcb]
2021-03-14 update DCDC layout
    [ESC_4in1_G071_1S3_SIZ200_badDCDC.kicad_pcb]
2021-03-15 adjust motor pad connection polygons
    [ESC_4in1_G071_1S3_SIZ200.kicad_pcb]
2021-03-27 add aisler compatible layout
    [ESC_4in1_G071_1S3_SIZ200.kicad_pcb, ESC_4in1_G071_1S3_SIZ200_badDCDC.kicad_pcb]
2021-04-19 general redesign 1 current sensor per ESC
    [ESC_4in1_G071_1S3_SIZ200.kicad_pcb, ESC_4in1_G071_1S3_SIZ200.sch, ESC_4in1_G071_1S3_SIZ200_90deg_aisler.kicad_pcb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]
2021-04-23 layout work
    [ESC_4in1_G071_1S3_SIZ200.kicad_pcb]
